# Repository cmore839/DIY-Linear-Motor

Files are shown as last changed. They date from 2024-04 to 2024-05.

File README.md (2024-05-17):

# DIY-Linear-Motor
Official Discord (https://discord.com/invite/5FmVrjaZHb)

https://www.youtube.com/watch?v=wEBWoIjgftI

This is an attempt to make a high performance and low cost linear motor for the diy hobby user. This can be adapted to any use case as needed, 3D printer, pick and place etc. See here for background on operating principle.

Performance: A 6 coil forcer was able generate peak of 16N of force. This can't be sustained for long as the coils would eventually melt.

https://en.wikipedia.org/wiki/Linear_motor

## Research and Sim (coil and magnet) + Market Options

First steps was research exisiting designs and perform simulations where possible. 

The following two projects were very helpful in the early stages:
- https://www.instructables.com/DIY-IRONLESS-LINEAR-SERVO-MOTOR/
- https://github.com/TkkrLab/LinearMotor

Summary of coil and magnet pitch is also as follows.
Since there is conflicting arrangements of coil and magnet pitches based on the information available some simulation was required. Using Ansys electrical some key parameters were discovered, both flat and round motor designs were tested but only the round was pursued further due to the easier construction techniques. Starting with permanent magnets and the magnet tube, there is commercially available 13mm OD - 12.1mm ID aluminium tube https://tinyurl.com/5435frky that is available for hobby plane builds, this can be purchased locally in 1m lengths and bears the label KS Precision Metals from USA. Therefore 12mm OD permanent magnets fit snugly inside with little wasted space. The available lengths of 12mm permanent magnets vary from 15-30mm, this sets the both the magnet pitch and the coil pitch which affects the overall length of the forcer and available stroke. I decided to go with 20mm long magnets, which makes the N-N magnet pitch at 40mm. Inputing this into the simulation, the coil design was refined until a clean three phase back EMF was obtained, this was an iterative process that ended up with a coil spacing of 6.8mm. Once the spacing of the coils and magnets were fixed, optimisation of the number of turns and wire gauge was next. A target for maximum force to amperage ratio was slightly preferred over force to weight ratio. Using some initial parameters set by the motor driver (more details below), the phase to phase resistance should be greater than 10 ohms, with a design voltage of 35V means peak current would be approximately 3.5 amps, with the motor driver capable of 5 amp peak. Starting off with one set of three coils, each coil should provide 5 ohms of resistance, using the website (coil24) ID is fixed at 14mm to allow for clearance to the 13mm magnet tube, coil width is set to 6.35mm so wiring and the 6.8mm spacing can be honoured (more details later). Different wire gauges were tested keeping the above parameters the same and changing the number of turns to suit. This was repeated for dual and triple coils in series but with invertred winding direction. The summary of the findings are below.


The dual coil set was picked since the efficiency of force/amperage was quite high without going to the extra effort of make 9 coils for a triple set.

## Electronics Market

Alot of this project was enabled by the keen interest in the Arduino-FOC project being run over at https://docs.simplefoc.com/. There is a huge amount of information and support to get normal motors running in closed loop with great performance. I was keen to try and get a linear motor running using the same platform.

After some learnings and process of elimination the best combination of electronics was followings
- Ardunio brain: STM32 NUCLEO-G474RE
- Motor Driver SimpleFOCShield v2.0.4 (Aliexpress): https://docs.simplefoc.com/arduino_simplefoc_shield_showcase
- Encoder (Aliexpress): HEDS9740 360LPI

The NUCLEO-G474RE is the workhorse of the STM32 family with the highest clock speed and has been fully backwards compatible with SFOC library up to date.

Motor driver is based on the L6234 from ST, this is a well known chip which has a really nice implementation on the SFOC Shield with built in current sensing. In addition it has voltage regulator and an optimised layout which made me not reinvent the wheel on this aspect.

In order for closed loop control to be sucessful a linear encoder is needed the HEDS9740 360LPI was chosen due to the cost and performance ratio. In quadrature mode, a single step should be 17 micrometers, for bigger budget projects the RLS magnet strip and board level incremental encoder would be great, this could give 5 micron step size.

## Mechanical build (electronics below)

Magent tube - this was relatively straightforward, I decided to super glue two individual magents together to reduce the overall length that needed to be compressed, this was a small jig in a vice made out of PE so the glue wouldn't stick, it was debatable if this was worth it. Next was to insert all of the magnets into the aluminium tube with one end capped with tape and a wooden dowel inserted first to move the first magnet away from the end of the tube. With a liberal amount of 2 part epoxy placed in the tube and on each magnet, the magnets are all placed in the same pole facing one another, this means a clamping force is required overnight while the glue sets, a simple woodworking clamp did the trick.

### Coils - Mechanical

Since this is a round linear motor, the winding process was slightly easier than a rectangular flat coil for a u-shaped linear motor. It took quite a lot of trial and error even to get a average looking coil, this all required testing different glues and jigs. I ended up using my 3 axis CNC router with a servo as a spindle, this essentially gave me a very large coil winding machine. The coil arbors we're made out of HDPE with a shoulder screw being the central core giving strength and straightness. The wire needs a guide close to the arbor as well as a way of adding tension to the system. In the end I used an old inflatable ball needle for the wire guide and a cloth in a vice provided the winding tension. https://youtu.be/FTWShWmTZQY The coil I ended up making was the following:

Coil

As I was using the CNC router I just wrote a gcode to do the coil winding number of turns while moving a single axis along the pitch of the coils and tweaked it from there if the coil jumped or didn't fill properly. This turned out to be very difficult, especially since it has 16 layers and 249 turns, getting everything sitting perfectly was fairly unachievable. I eventually got a code that worked okay as well as working on the basics need for the arbor design and the glue needed, since the coil needs constant tension or else it will unwind, I ended up using a two part epoxy that was applied between every layer while winding this had to sit overnight, and once set, placing the arbor in the freezer for 5 mins freed the copper coil easily. Other glues that I tried and failed were superglue, nail varnish and timber varnish. Once you have your six coils done with about 10 cm of flying lead on each end I assembled them together and then wired up in sequence. See schematic below for an overview of mechanical layout and electrical wiring.



In order to get the coils spaced to the simulation value, I used small hole punch circles of plastic to sit between each layer, these were superglued in place as a temporary holder to achieve the 6.8mm coil pitch, this needs to be done for each coil and then placed in the correct configuration (see layout drawing of coil polarity). Note: A stack of three coils is 20mm even though the pitch above is 6.8mm. So overall your 6 coils will be a nice 40mm long. For my prototype I aligned the six coils of the internal diameters with another HDPE Arbor, this ensured the clearance around the magnet tube is kept even without scratching. I used some more two part epoxy to set this all in place. Soldering the ends of each coil in series and delta Y configuration is again as per the coil layout drawing, leaving just the three phases A,B,C for connection to the motor driver.

## Assembly

The coil set sits on a small mgn9 linear bearing carriage and rail, I machined some small brackets from acrylic sheet, this held the magnet tube in place and secured the coils over the whole length of travel. There is plenty of room for improvement in the brackets, but for a prototype this wasn't the priority. The linear encoder head was attached to the moving carriage and the encoder strip was attached to the magnet tube end brackets, one end was a M3 countersunk screw and the other end was a wire flexure that kept the strip tight. Cable strain relief was a problem which needed to be paid attention to, mostly due to the sensitive pin terminations on the encoder; this was fixed later with an encoder breakout board (see picture).

NOTE: I found out the hard way that even stainless steel bolts are affected by the permanent magnets too strongly and cause issues. Where possible any screws that are on the moving carriage need to be either plastic or aluminium screws.

# Motor driver - Setup and First Run (SimpleFOC)

A Lot of this project was centered around the possibility of getting the SimpleFOC Arduino library working with a linear motor, given the limited information this was tricky to navigate initially. Hopefully this helps with other people trying to get up and running. (There is some assumed knowledge that I won't touch on, with the SFOC website and forums being very helpful).

Once you've got the SFOC library installed as well as the STM32 offical library from STMicro (very important), you are ready to do some pre-checks and calibration.
### Encoder Check (Don't SKIP)
Under the SFOC example list, utilities, sensor test, and select your appropiate encoder, in this case just standed AB encoder. This checks the pinout for your encoder (and you can ignore the CPR number for now, just leave as default). Once you get a decent position and velocity curve like demonstrated here moving by hand (https://youtu.be/7zi0S_LTSNg) you can continue to pole pair.
### Pole Pair Calibration
Under the SFOC example list, utilities, calibratrion, find pole pairs, encoder, launch the find pole pairs number test code (FPPN). Here we're trying to find a specific number for the encoder CPR that gives us a round number when running the FPPN code. Starting with (1) in the BLDCMotor line, add in your 3PWM driver phase and enable pinouts, as well as your encoder pinouts your verified above. With a best guess CPR number put into last variable of the encoder settings. Run this code and wait for it to complete. What the script is doing is checking running the coils in open loop angle mode and counting the number of encoder pulses (encoder angle), what we want is for the numbers calculated to be a nice round number!

For example (using a reduced pp_search_angle = 3*PI as my motor is too short)

PP = Electrical angle / Encoder angle 

Encoder CPR = 1110, PP = 540.00/-272.27=-1.98, Close but the encoder angle isn't a round number.

Encoder CPR = 1130, PP = 540.00/-267.53=-2.02, Close but the encoder angle still isn't a round number.

Encoder CPR = 1120, PP = 540.00/-270.00=-2.00, Perfect encoder angle.

So for the final code, the BLDCMotor and encoder line will look like this:

BLDCMotor motor = BLDCMotor(2);

Encoder encoder = Encoder(PC8, PC6, 1120); //Pinout may vary.

### Adding the rest
After that is complete the rest is plug and play with standard SFOC library. Start out with voltage based, torque closed loop, ideally using commander and SFOC Studio to monitor and tune the motor. Then move to voltage base angle control. Then lastly FOC_Current angle control, there was a trick with the inline current sense that I found which required the third term to need the _NC, rather than just leaving it default.

### Klipper Interface
In order to use this motor driver with an exteral controller I'm using the step/dir listener provided by the SFOC community, this works great as long as you can keep the electrical noise low and speeds at a reasonable limit (more testing needed!). https://youtu.be/fjbZ5hjDKrU

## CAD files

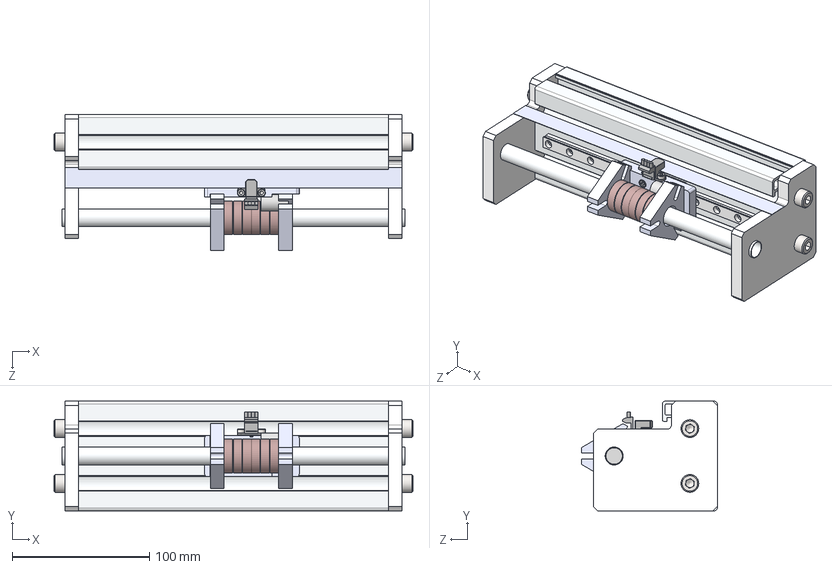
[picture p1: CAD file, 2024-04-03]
DIY Linear Motor - CAD.STEP
262.0 x 80.0 x 98.9 mm
40 x 80 Stick Proto_Short 1<As Machined>
Copy of v1_MGN9_250^Copy of MGN9_Proto Axis v2___ _________
Copy of v1_MGN9-H^Copy of MGN9_Proto Axis v2___ _________
Alu Tube Proto
12x20 Neo Mag x 10
3 Phase Coil x 2
HEDS Encoder
Encoder Strip Proto
Part1^Proto Axis v2 x 2
Modular Coil Cap x 2
MGN Adapter Coil
B18.3.1M - 3 x 0.5 x 10 Hex SHCS -- 10NHX_B18.3.1M - 3 x 0.5 x 10 Hex SHCS -- 10NHX x 6
B18.3.1M - 8 x 1.25 x 16 Hex SHCS -- 16NHX_B18.3.1M - 8 x 1.25 x 16 Hex SHCS -- 16NHX x 4
B18.3.1M - 3 x 0.5 x 5 Hex SHCS -- 5NHX_B18.3.1M - 3 x 0.5 x 5 Hex SHCS -- 5NHX x 2

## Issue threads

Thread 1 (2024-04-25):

Just dropping in to say hi, and this is awesome!

Ben-PH, 2024-04-25:
Love this project. It's something that I've been wanting to do for a while. I got a magnet assembly sorted, and have a rotary encoder on order. I see that you've gone about position encoding in a much nicer way, I think.

I would like to build something like this myself, though with some slight differences. would you be happy to get in touch over discord or something?

cmore839, 2024-04-26:
Hey, thanks for saying hello, sounds awesome, would be great to see more. Discord is already started, you can find us at https://discord.gg/MjB4ArvR

Closed 2024-07-10.

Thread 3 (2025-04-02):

Not a issue but want to discuss a project

elliotaldarson1717, 2025-04-02:
Hello,
I want to discuss similar project but commercial product with very high accuracy like Peopoly Magneto X . If possible email me elliotaldarson1717@gmail.com

cmore839, 2025-04-03:
Hello, please use the discord link to discuss any projects or ideas cheers.

Closed 2025-04-03.

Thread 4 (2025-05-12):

Help for running motor

Wawavoun, 2025-05-12:
Hi,

Great thanks for the share of your project.

We have build the motor and now are in trouble.

Sensor check look good as we see movements on both curves.

Find PP give very similar results that yours but we notice some irregular results.
Here the motor move nicely.

TRY ONE

Estimated PP : 2
PP = Electrical angle / Encoder angle
540.00/225.00 = 2.40

If PP is estimated well your motor should turn now!
 - If it is not moving try to relaunch the program!
 - You can also try to adjust the target voltage using serial terminal!
MOT: Align sensor.
MOT: sensor_direction==CW
MOT: PP check: OK!
MOT: No current sense.
MOT: Ready.

TRY TWO

Estimated PP : 2
PP = Electrical angle / Encoder angle
540.00/270.48 = 2.00

If PP is estimated well your motor should turn now!
 - If it is not moving try to relaunch the program!
 - You can also try to adjust the target voltage using serial terminal!
MOT: Align sensor.
MOT: sensor_direction==CW
MOT: PP check: fail - estimated pp: 4.33
MOT: No current sense.
MOT: Ready.

Using the code provided here the motor move  little bit but with loud and strong vibration and we get :

TRY ONE

MOT: Monitor enabled!
MOT: Align sensor.
MOT: sensor_direction==CCW
MOT: PP check: fail - estimated pp: 28.72
MOT: Zero elec. angle: 5.93
MOT: Align current sense.
CS: Switch A-B
CS: Inv A
CS: Err align B
MOT: Align error!
MOT: Init FOC failed.
0.0000	0.0000	-326.5935	-0.5708

TRY TWO

MOT: Monitor enabled!
MOT: Align sensor.
MOT: sensor_direction==CCW
MOT: PP check: fail - estimated pp: 56.71
MOT: Zero elec. angle: 2.43
MOT: Align current sense.
CS: Switch A-B
MOT: Success: 2
MOT: Ready.
0.0000	-12.0000	70.4307	1.9383

Using Simplefocstudio give communications with the Nucleo board but no way to get a move probably due to failed init of SimpleFOC.

We understand its not easy to help with only partial information but may be this will talk to you and give some ideas where to search the problem.

Thanks.
Philippe

cmore839, 2025-05-12:
Hi Philippe, can you share details on the discord? Things like photos, spec of the motor and encoder (if different from the original design) and your code would really help!

For the PP search, you can increase the electrical search angle so instead of 540degress, try doubling it to gather more data.. If you are using the exact same motor and encoder as the build then you can basically skip this step and use my example code.

Wawavoun, 2025-05-13:
Thanks for trying to help.

You can find some videos, used code and also log files here :
https://drive.google.com/drive/folders/1c_YxLfV6ejki6G99F5b-Rauth2--lkrq?usp=sharing

If I can give more details please ask !

We have try to build the motor as your and follow the bom, same sensor, same boards etc...

What I can say about the build is as follow
_ the mechanic is not perfect and there is some light frictions
- the total length of the 6 coils is 41 mm due to fabrication tolerances and so on
- all coils have 227 turns except one which have 207 turns due to lack of wire at winding the last one...

Again thanks for the help.
Philippe

cmore839, 2025-05-14:
Your open loop PP find looks good, so driver and motor should be okay. 2 things to try. For the encoder, use the example code to do a serial plot and watch the position and velocity on the screen while moving the motor by hand, I have had a encoder turn up dead once before, in addition if for AB encoders sometime wiring can cause noise.. I try to use shielded twisted pairs on my AB signals where possible. If encoder is definitely working, then it could be tuning and settings.. Try closed loop torque mode using voltage as the torque mode (not FOC current) then start playing from there.. As the docs say for new motors you need to start basic and work up.

Wawavoun, 2025-05-14:
I have do some improvement to the mechanic and get now more consistent results for PP find. I have see that the alu tube also move during trial so I clamp it now between the motor flanges.

I am a point where SimpleFOCstudio seems to work and give some results. For example if I disable the motor, move it by hand and them enable it he come back to the exactly the initial position...
I have always some vibrations and will do some CEM improvement asap.

The strange thing is that when I put fe M200 into the command line I see the red "target" field momentary change to 200 and then come back to 0 and but I dont see any move... What is the command I should put in to get a move ?

Also in SimpleFOCstudio I also noticed that the red angle field move from ~ -5 to +5 (rad ?, deg ?) from one end of the motor to the other end (with motor disabled and moving by hand). Again is that normal ?

Thanks
Philippe

cmore839, 2025-05-15:
You might need to disable the step/dir listener code, if you are using my example to get started.. What you are doing is correct, but it just requires careful setup.. Sometimes it is easier to start from fresh code, then add little by little so you know what each bit does.. And yes -5 to +5 rad is fine, since default is rotary BLDC motors it is all written with that in mind.. You can change to linear with code mods somehow but I haven't bothered.

Wawavoun, 2025-05-15:
I have disabled all the code marked as 'comment out when using the commander'.

I look really like if the move command 'Mxx' is not taken in account by the Nucleo.

After removing the step/dir listener code how is updated "received_angle" via serial com in your code ?

Thanks.
Philippe

cmore839, 2025-05-16:
You can try and delete the received_angle text and just leave empty brackets.. That should work I think, but it is a long time since playing with that.

Wawavoun, 2025-05-16:
With this modification in the code it works !

I can move the engine with M command and also with jog control into simplefocstudio.

Great thanks for the help and for sharing your design.
Philippe
